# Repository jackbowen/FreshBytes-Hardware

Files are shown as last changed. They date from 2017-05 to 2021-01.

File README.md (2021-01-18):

# FreshBytes Hardware

All of the hardware needed to run FreshBytes, a hydroponic and aquaponic monitoring and control system. The system runs on [this software](https://github.com/jackbowen/FreshBytes-Backend) and is interacted with through [this app](https://github.com/jackbowen/FreshBytes-WebApp).

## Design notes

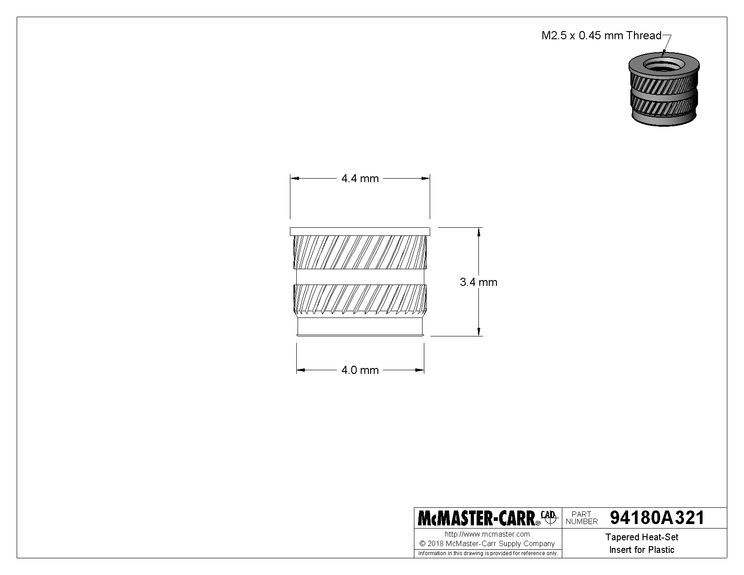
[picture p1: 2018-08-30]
Datasheets/94180a321_heat-set inserts for plasticsl.gif

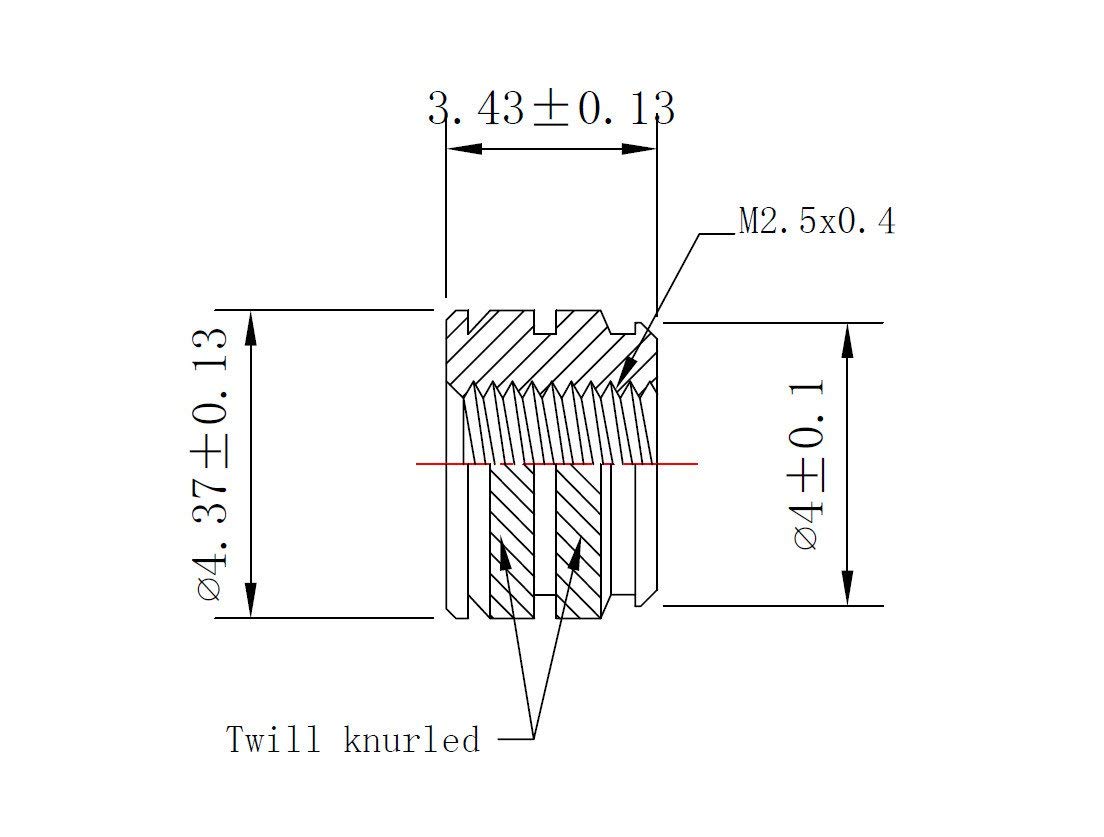
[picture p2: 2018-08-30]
Datasheets/51dJ2v1S5CL._SL1104_.jpg

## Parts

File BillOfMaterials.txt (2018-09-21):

+-------------------+
| BILL OF MATERIALS |
+-------------------+

The following is a list of all the parts required to construct the FreshBytes
system. They are organized by the distributor which the parts are purchased 
from. 

+-----------------------------------------------------------------+
| DISTRIBUTOR: DIGIKEY                                            |
+--------------------------------+---------------------+----------+
| Part Name                      | Part Number         | Quantity |
+--------------------------------+---------------------+----------+
| 40 Pos Headers                 | ???????             | 1        |
| 9 Pos Din Cable                | 839-1054-ND         | 1        |
| 9 Pos Mini Din Connector       | CP-2290-ND          | 1        |
| 4x1 MUX                        | 568-10088-1-ND      | 1        |
| Power Receptacle - Main        | Q219-ND             | 1        |
| Power Receptacle - Accessories | 486-1343-ND         | 2        |
| AC DC Converter                | 945-1401-5-ND       | 1        |
| Relay                          | PB1014-ND           | 2        |
| Power Chord                    | Q103-ND             | 1        |
| 200 Ohm 0805 Resistor          | RMCF0805JT200RCT-ND | 2        |
| 470 Ohm 0805 Resistor          | RMCF0805JT470RCT-ND | 4        |
| 3.3k Ohm 0805 Resistor         | RMCF0805JT3K30CT-ND | 2        |
| 4.7k Ohm 0805 Resistor         | RMCF0805JT4K70CT-ND | 1        |
| 10k Ohm 0805 Resistor          | RMCF0805JT10K0CT-ND | 2        |
| PC817 Opto-isolator            | 425-2774-1-ND       | 2        |
| 2N2222 Transistor              | ???????             | 2        |
| 2 Pos Screw Terminal           | A121350-ND          | 1        |
| 1N4148 Diode                   | 1N4148FS-ND         | 2        |
+--------------------------------+---------------------+----------+

TODO: these numbers only take into account PCB enclosure and not probe.
+-----------------------------------------------------------------------------------------+
| DISTRIBUTOR: MCMASTER-CARR                                                              |
+----------------------------------------------+-------------+----------------------------+
| Part Name                                    | Part Number | Quantity                   |
+----------------------------------------------+-------------+----------------------------+
| M4 x 0.7 mm 12mm Stainless Steel Flat Head   | 93395A257   | 1                          |
| M4 x 0.7 mm Stainless Steel Nut              | 94150A335   | 1                          |
| M2.5 x 0.45 mm 3mm Steel Rounded Head Screw  | 92005A052   | 1                          | <-TODO: got the A053
| zinc-plated steel nut for M2.5x0.45mm screw  | 90591A113   | 1 (bag of 100 - we need 9) |
| M2.5 x 0.45 mm 8mm Stainless Steel Flat Head | 91801A137   | 1                          |

| 10mm steel rounded head screw - M2.5x0.45mm  | 92005A071   | 1 (bag of 100 - we need 3) | <-TODO: check these are correct size
| 5mm aluminum spacer for M2.5 screw           | 94669A098   | 4                          |
| 3.4mm threaded heat set inserts - M2.5x0.4mm | 94180A321   | 1 (bag of 100 - we need 4) |
| 7.9mm threaded heat set inserts - M4x0.7mm   | 94180A353   | 1 (bag of 50 - we need 6)  |
+----------------------------------------------+-------------+----------------------------+

+-------------------------------------------------------------------------------+
| DISTRIBUTOR: AMAZON                                                           |
+--------------------------------------+-------------+--------------------------+
| Part Name                            | Part Number | Quantity                 |
+--------------------------------------+-------------+--------------------------+
| M2.5 x 0.4 threaded heat set inserts | B0763FH6NG  | 1 (bag of 20, we need 4) |
+--------------------------------------+-------------+--------------------------+

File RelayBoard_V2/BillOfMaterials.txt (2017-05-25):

+-------------------+
| BILL OF MATERIALS |
+-------------------+

The following is a list of all the parts required to construct the FreshBytes
system. They are organized by the distributor which the parts are purchased 
from. 

+-----------------------------------------------------------------+
| DISTRIBUTOR: DIGIKEY                                            |
+--------------------------------+---------------------+----------+
| Part Name                      | Part Number         | Quantity |
+--------------------------------+---------------------+----------+
| 40 Pos Socket to Cable         | H1CXS-4036G-ND      | 1        |
| 40 Pos Female Socket to Cbl    | AE11124-ND          | 1        |
| 40 Pos Male Socket to Board    | S9175-ND            | 1        |
| 9 Pos Din Cable                | 839-1054-ND         | 1        |
| 9 Pos Mini Din Connector       | CP-2290-ND          | 1        |
| 4x1 MUX                        | 568-10088-1-ND      | 1        |
| Power Receptacle - Main        | Q210-ND             | 1        |
| Power Receptacle - Accessories | 486-1343-ND         | 2        |
| AC DC Converter                | 945-1401-5-ND       | 1        |
| Relay                          | PB1014-ND           | 2        |
| Power Chord                    | Q103-ND             | 1        |
| 200 Ohm 0805 Resistor          | RMCF0805JT200RCT-ND | 2        |
| 470 Ohm 0805 Resistor          | RMCF0805JT470RCT-ND | 4        |
| 3.3k Ohm 0805 Resistor         | RMCF0805JT3K30CT-ND | 2        |
| 4.7 k Ohm 0805 Resistor        | RMCF0805JT4K70CT-ND | 1        |
| PC817 Opto-isolator            | 425-2774-1-ND       | 2        |
| 2N2222 Transistor              | ?                   | 2        |
| 2 Pos Screw Terminal           | A121350-ND          | 1        |
| 1N4148 Diode                   | 1N4148FS-ND         | 2        |
+--------------------------------+---------------------+----------+

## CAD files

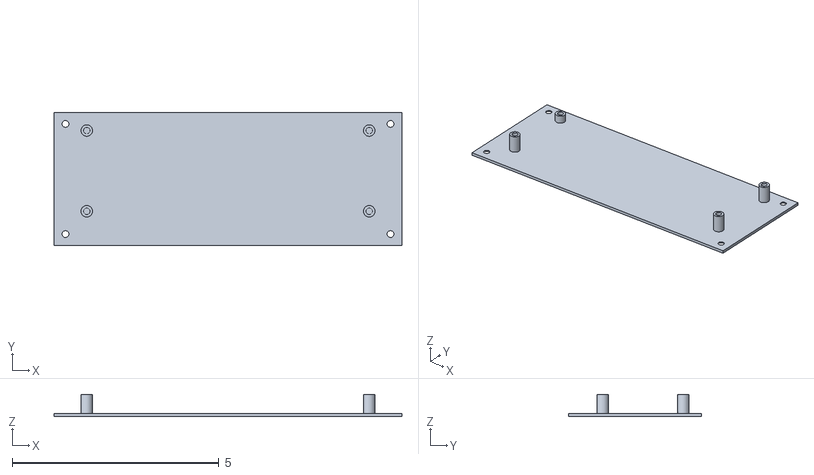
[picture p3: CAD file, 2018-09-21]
Enclosure/EnclosureModel/Enclosure Bottom.stl
8.41 x 3.22 x 0.541

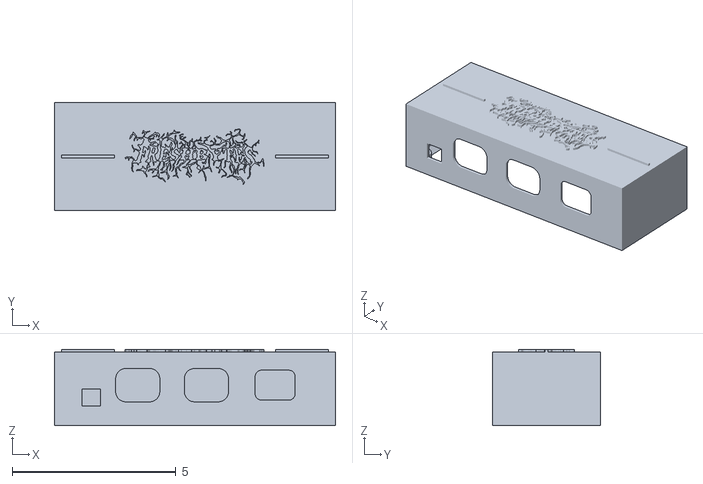
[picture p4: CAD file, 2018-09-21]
Enclosure/EnclosureModel/Enclosure Top.stl
8.59 x 3.31 x 2.33

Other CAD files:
Enclosure/EnclosureModel/3d Model.3dm
Enclosure/ToBeDeleted/ExplodedView.3dm

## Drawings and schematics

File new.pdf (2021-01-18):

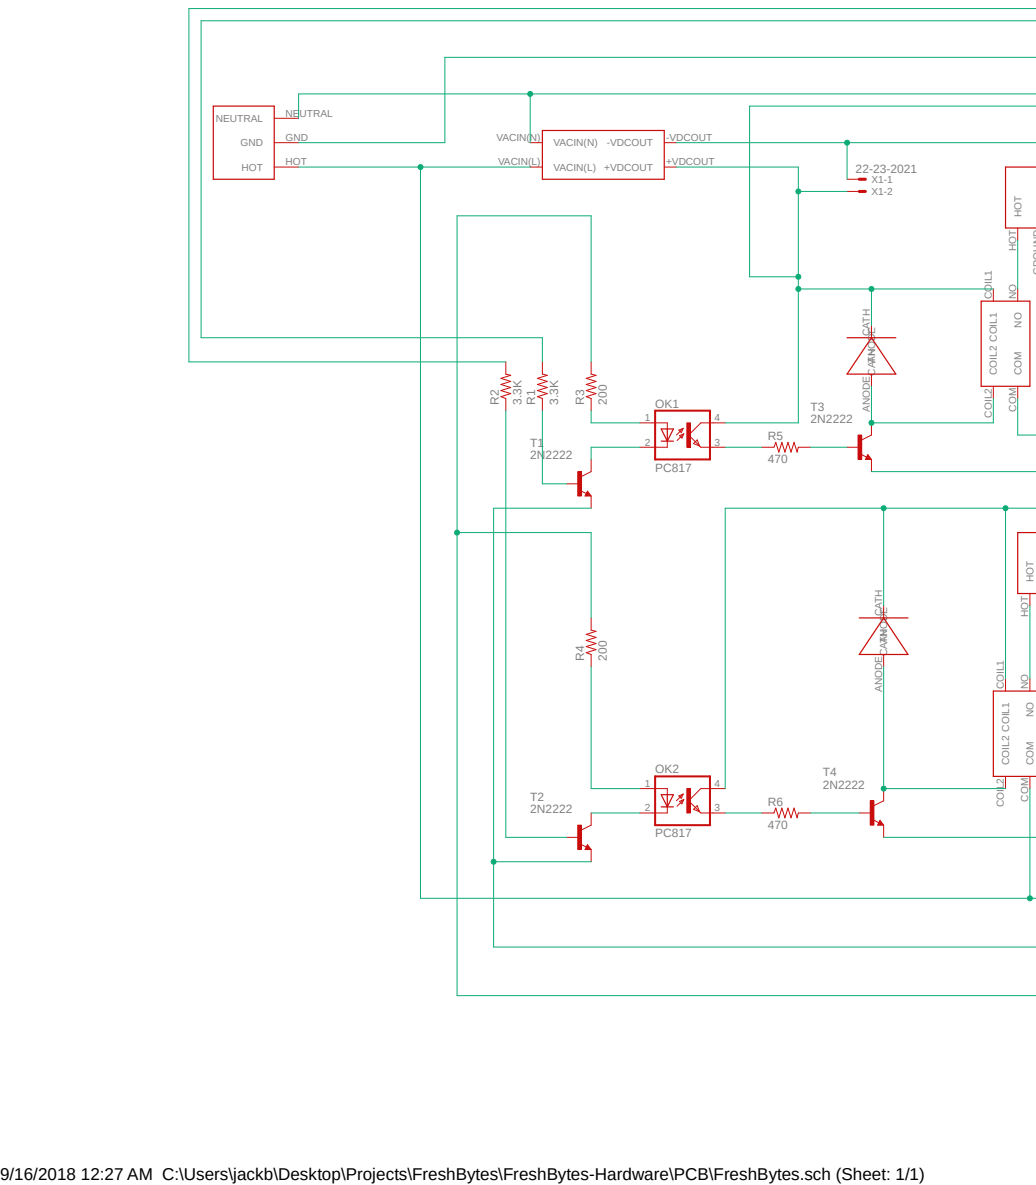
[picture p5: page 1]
9/16/2018 12:27 AM C:\Users\jackb\Desktop\Projects\FreshBytes\FreshBytes-Hardware\PCB\FreshBytes.sch (Sheet: 1/1) ³.3K; VACIN(N) VACIN(N); VACIN(L) VACIN(L); -VDCOUT; +VDCOUT; GROUND HOT HOT; HOT HOT; NEUTRAL; NEUTRAL GND; GND; HOT; COIL1 COIL1; NO NO COIL2 COIL2; COM COM COIL1 COIL1; COM COM

4 CATH CATH ANODE ANODE CATH CATH ANODE ANODE

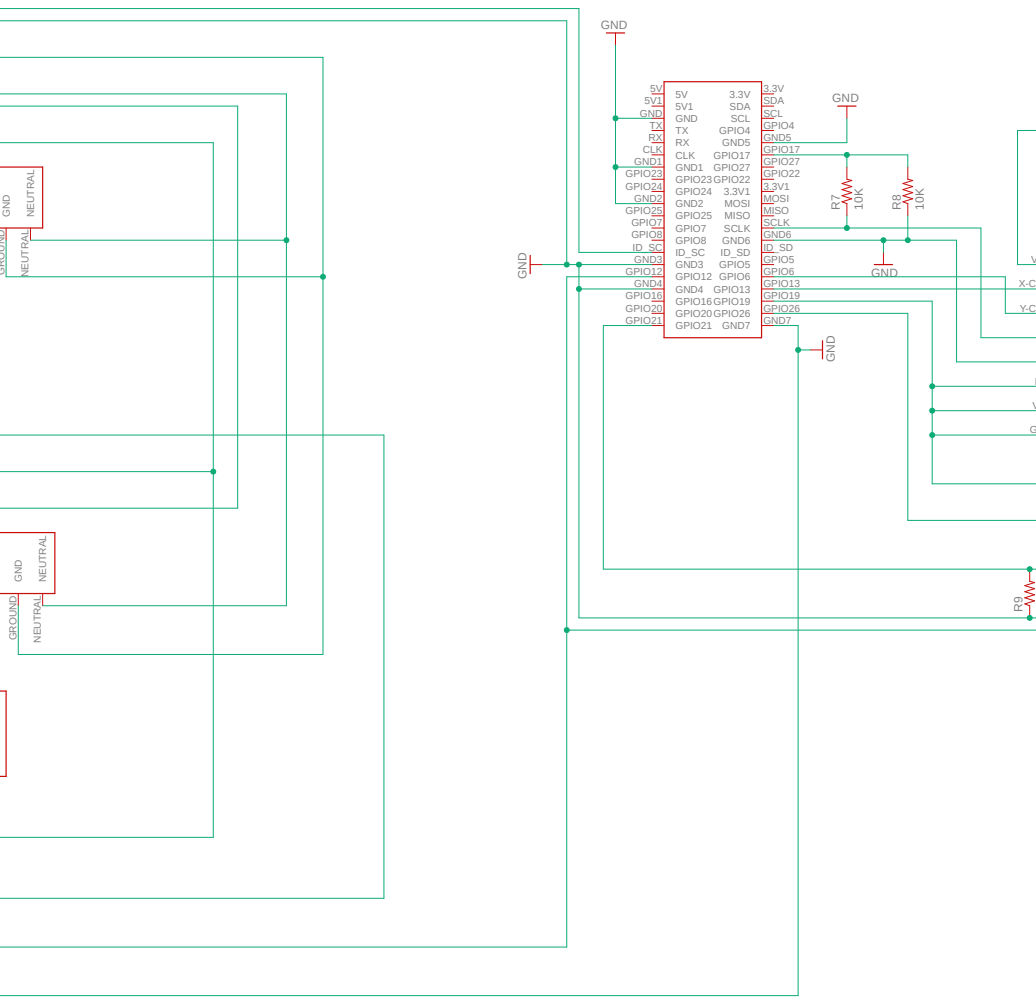
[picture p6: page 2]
GND GND; GND; Y-COM; INH; VEE GND; VCC; X-COM R⁷; R⁹ NEUTRAL NEUTRAL GND; NEUTRAL NEUTRAL GND GROUND; SDA; SCL; SCL GPIO4; GPIO4 GND5; GND5 GPIO17; GPIO17 GPIO27; GPIO27 GPIO22; GPIO22; 3.3V1 MOSI; MOSI MISO; MISO; SCLK; SCLK GND6; GND6; ID_SD GPIO5; GPIO5 GPIO6; GPIO6 GPIO13; GPIO13 GPIO19; GPIO19 GPIO26; GPIO26 GND7; GND7; CLK CLK; GND1 GND1; GPIO23 GPIO23; GPIO24 GPIO24; GND2 GND2; GPIO25 GPIO25; GPIO7 GPIO7; GPIO8 GPIO8; GND3 GND3; GPIO12 GPIO12; GND4 GND4; GPIO16 GPIO16; GPIO20 GPIO20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

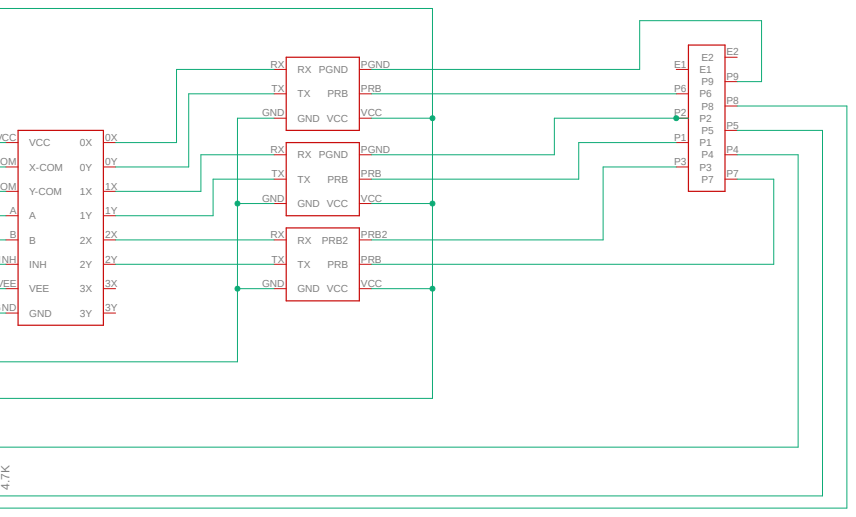
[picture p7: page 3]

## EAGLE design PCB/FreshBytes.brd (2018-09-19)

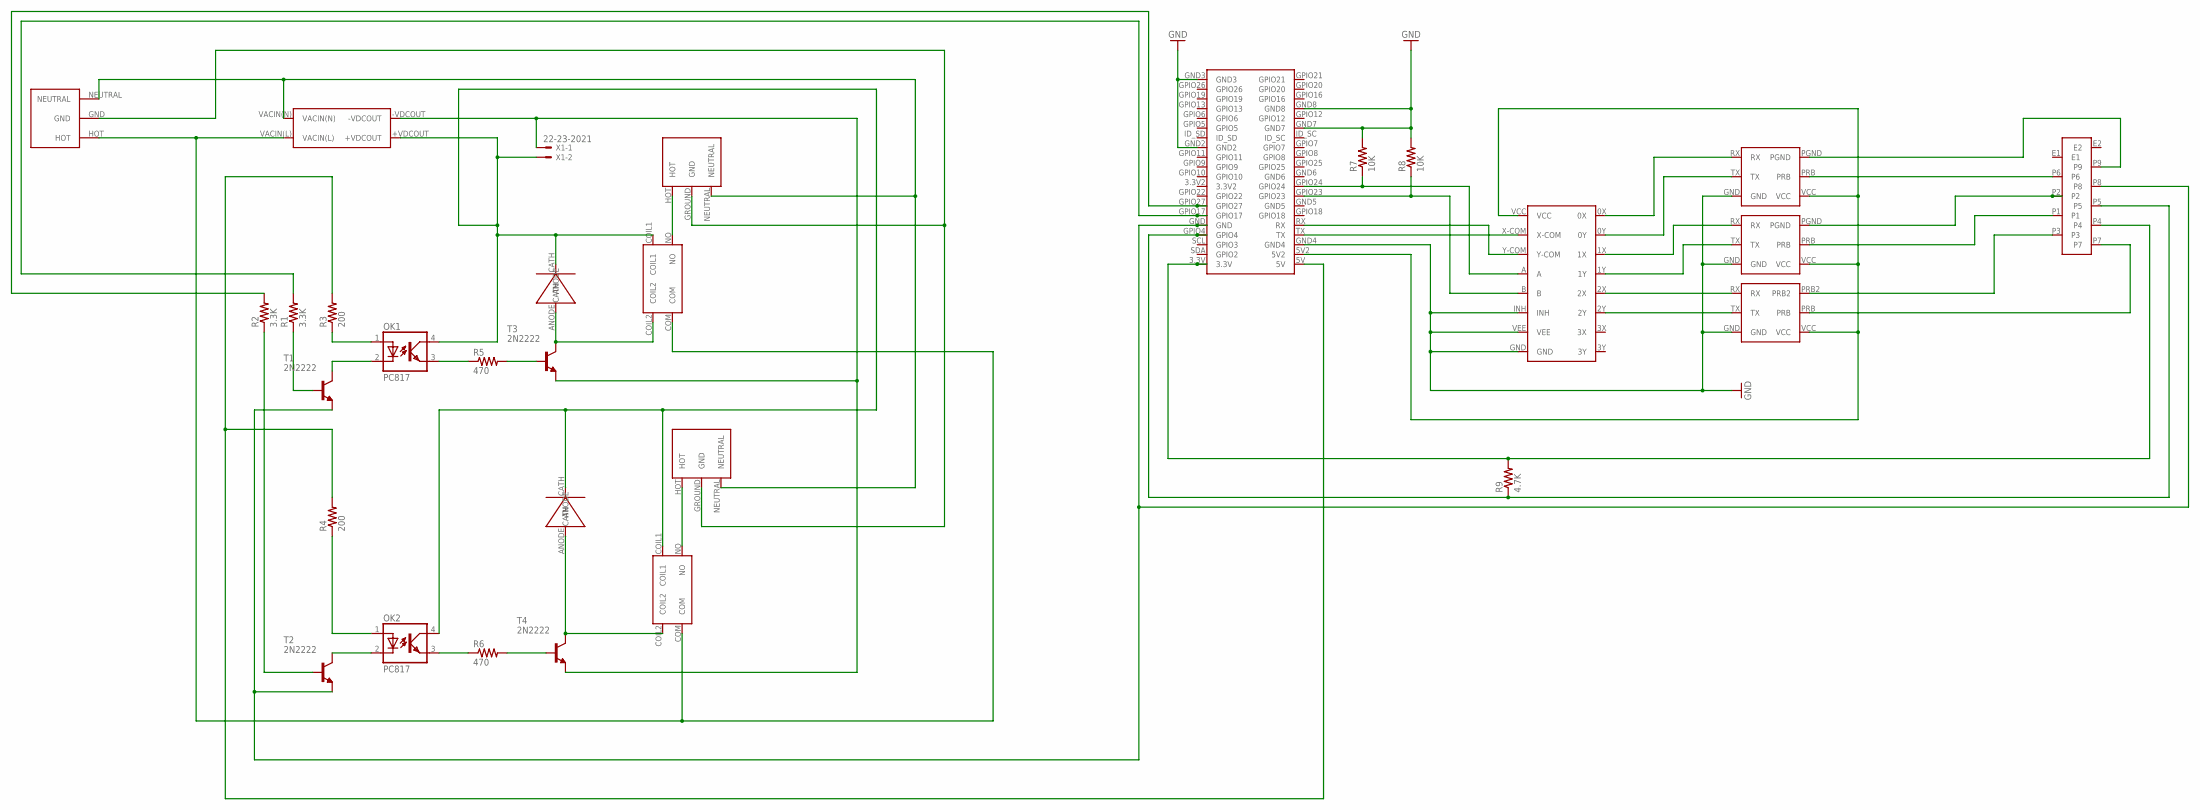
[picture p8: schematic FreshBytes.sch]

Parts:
MUX: 7HC4052_MUX; SSOP16
OK1, OK2: PC817; DIL04
R1, R2: 3.3K; R0805
R3, R4: 200; R0805
R5, R6: 470; R0805
R7, R8: 10K; R0805
R9: 4.7K; R0805
T1, T2, T3, T4: 2N2222; TO92-EBC-OVAL
U$1: POWER_IN
U$2, U$3: VTB8441BH
U$4: 9POS_MINI_DIN
U$5: ATLAS_DO_WITH_ICON
U$6, U$7: IEC_FEMALE
U$8: ATLAS_PH_WITH_ICON
U$9: ATLAS_PPM_WITH_ICON
U$10: RPI_ZERO
U$11, U$12: RELAY
U$17: RAC02-05SC_ACDCCONVERTER
X1: 22-23-2021

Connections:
3.3V2: U$10.3.3V2
AGND: T3.E, T4.E, U$17.-VDCOUT, X1.1
DGND: T1.E, T2.E, U$4.P8, U$10.GND
GND: MUX.GND, MUX.INH, MUX.VEE, R7.2, R8.2, U$5.GND, U$8.GND, U$9.GND, U$10.GND2, U$10.GND3, U$10.GND4, U$10.GND7, U$10.GND8
GND5: U$10.GND5
unnamed: R2.2, U$10.GPIO27
unnamed: R1.1, T1.B
unnamed: OK1.1 (A), R3.1
unnamed: OK1.2 (C), T1.C
unnamed: MUX.X-COM, U$10.TX
unnamed: R2.1, T2.B
unnamed: U$6.HOT, U$11.NO
unnamed: OK2.1 (A), R4.1
unnamed: OK2.2 (C), T2.C
unnamed: OK2.3 (EMIT), R6.1
unnamed: OK1.3 (EMIT), R5.1
unnamed: R5.2, T3.B
unnamed: R6.2, T4.B
unnamed: T4.C, U$3.ANODE, U$12.COIL2
unnamed: U$7.HOT, U$12.NO
unnamed: T3.C, U$2.ANODE, U$11.COIL2
unnamed: U$1.HOT, U$11.COM, U$12.COM, U$17.VACIN(L)
unnamed: U$1.NEUTRAL, U$6.NEUTRAL, U$7.NEUTRAL, U$17.VACIN(N)
unnamed: MUX.Y-COM, U$10.RX
unnamed: MUX.2Y, U$9.TX
unnamed: MUX.2X, U$9.RX
unnamed: MUX.1Y, U$8.TX
unnamed: MUX.1X, U$8.RX
unnamed: MUX.0Y, U$5.TX
unnamed: MUX.0X, U$5.RX
unnamed: MUX.A, R7.1, U$10.GPIO24
unnamed: U$4.P9, U$5.PGND
unnamed: OK1.4 (COL), OK2.4 (COL), U$2.CATH, U$3.CATH, U$11.COIL1, U$12.COIL1, U$17.+VDCOUT, X1.2
unnamed: MUX.VCC, U$5.VCC, U$8.VCC, U$9.VCC, U$10.5V2
unnamed: R1.2, U$10.GPIO17
unnamed: R9.2, U$4.P4, U$10.3.3V
unnamed: U$4.P7, U$9.PRB
unnamed: U$4.P3, U$9.PRB2
unnamed: U$4.P1, U$8.PRB
unnamed: U$4.P2, U$8.PGND
unnamed: U$4.P6, U$5.PRB
unnamed: R9.1, U$4.P5, U$10.GPIO4
unnamed: MUX.B, R8.1, U$10.GPIO23
unnamed: R3.2, R4.2, U$10.5V
PGND: U$1.GND, U$6.GROUND (GND), U$7.GROUND (GND)

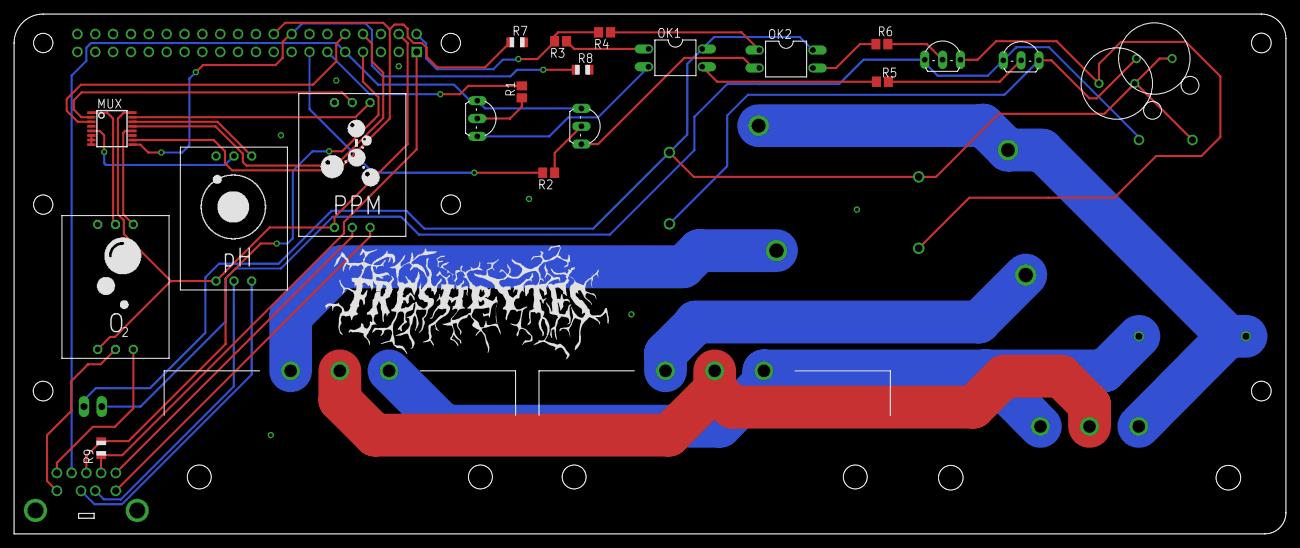
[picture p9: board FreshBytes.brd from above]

Board: 2 copper layers, 181.0 x 74.0 mm, 30 parts (1 on the bottom side), 43 nets.

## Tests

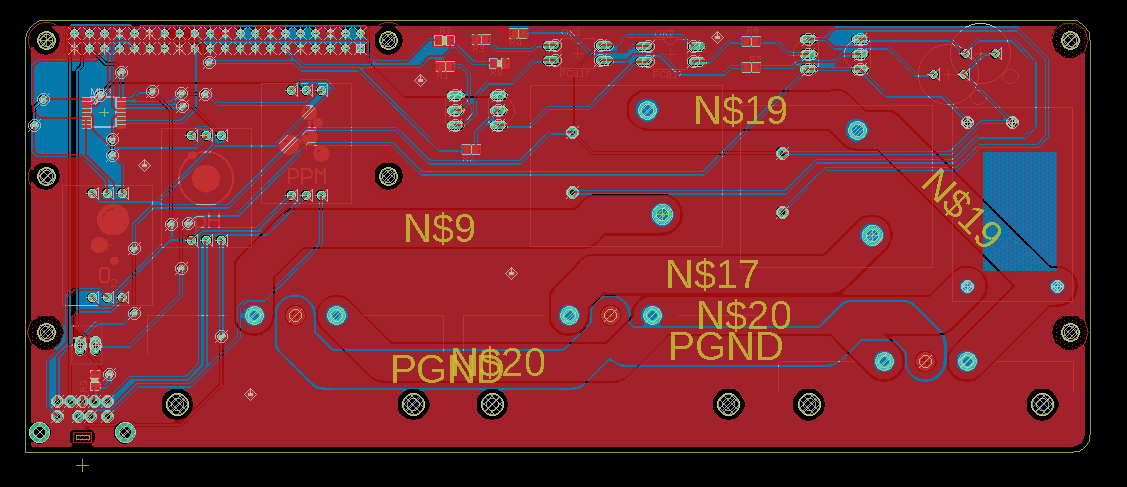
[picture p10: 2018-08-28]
Testing/pcb_pic.png

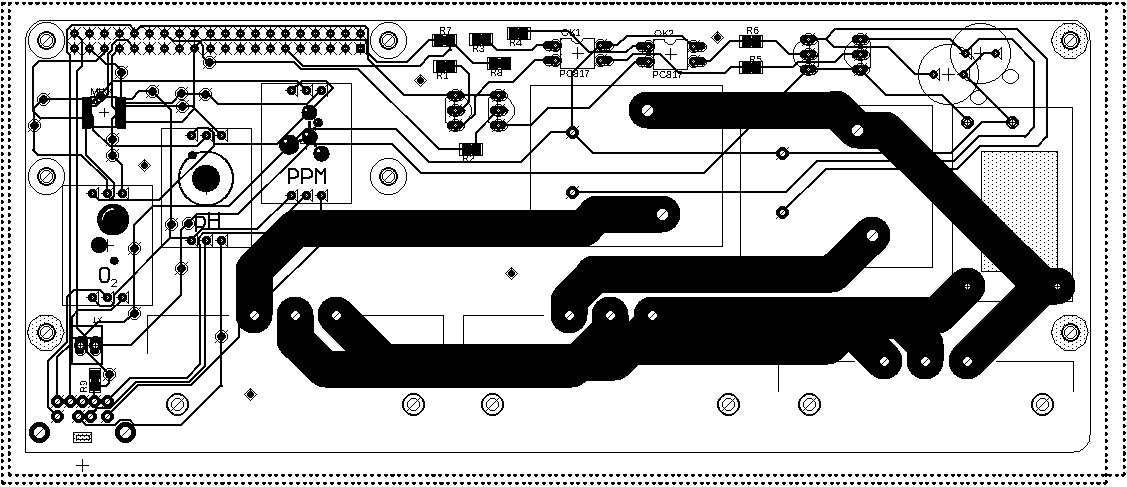
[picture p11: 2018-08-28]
Testing/pcb_bw_inverted.png

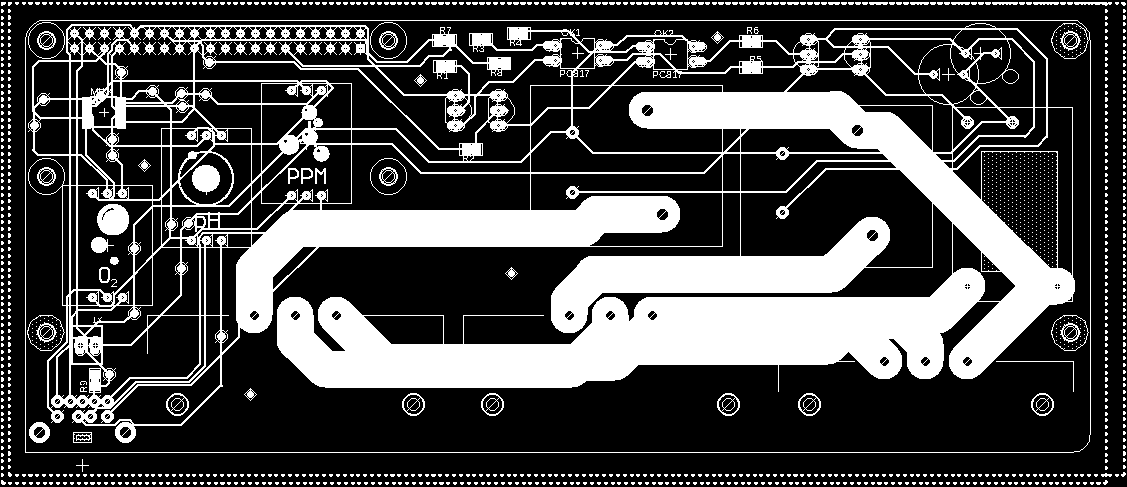
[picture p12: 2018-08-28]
Testing/pcb_bw.png

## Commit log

2017-05-10 finished schematic saved in Relayboard_2
    [relay.brd, relay.sch]
2017-05-12 Starting to work on enclosure
    [PCB_Enclosure.fcstd, RasPi-BplusHAT.brd, RasPi-BplusHAT.sch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]
2017-05-18 change power receptacles to thru hole
    [Enclosure.3dm, PCB_Enclosure.fcstd, ProbeEnclosure.3dm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]
2017-05-18 added bill of materials and moved 9 pos connector to proper location on brd. 40 pin connector and 1 of the female power receptacles are also in the correct y position
    [Enclosure.3dm]
2017-05-22 placed all components on board (not routed)
    [relay.brd]
2017-05-23 routed ac. 3mm extension on male power receptacle
    [relay.brd]
2017-05-25 flipped relays and repositioned power receptacles
    [relay.sch]
2017-05-25 update enclosure drawing and add diodes to bill of materials
    [Enclosure.3dm]
2017-05-31 Route everything. Add logo
    [relay.brd]
2017-06-01 GND pour and add gerbers
    [relay.brd, relay.sch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]
2017-06-02 Reduced DPI of silkscreen to OSH Park can actually fabricate them. New gerbers.
    [relay.brd, relay.sch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]
2017-06-02 decrease pad size for main connection
    [relay.brd, relay.sch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]
2017-06-16 update bill of materials and enclosure drawing
    [Enclosure.3dm]
2017-06-23 update enclosure drawing and add start of lid sketch
    [Enclosure.3dm, Enclosure_Bottom.stl]
2018-08-24 Swap to R Pi Zero W as the brains
    Power inlet may be in the wrong location. Will commit again tomorrow with proper spot.
    [Drawing1.dwg, Enclosure.3dm, Enclosure_Bottom.stl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]
2018-08-29 Add logo to BRD file, create gerbers, update BOM
    [ExplodedView.dwg, FreshBytes - Copy.brd, FreshBytes.brd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]
2018-08-30 Update CAD drawings
    [ExplodedView.dwg, ExplodedViewCopy.dwg]
2018-09-19 Fix drill size for RPi headers. Swapping over to Rhino for CAD stuff
    [ExplodedView.3dm, ExplodedViewCopy2004.dwg, FreshBytes.brd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]
2018-09-21 Add 3d printable enclosure
    [3d Model.3dm, AxonView.3dm, Drawing1.dwg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]
2018-09-21 Edit axon view in Inkscape to adjust fill colors and line weights
    [AxonView.3dm]
2018-09-25 Start of exploded axon view
    [3d Model.3dm, AxonSVG.3dm, AxonView.3dm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]
2021-01-18 Refine vector drawing
    [3d Model.3dm, AxonSVG.3dm, AxonView.3dm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]
